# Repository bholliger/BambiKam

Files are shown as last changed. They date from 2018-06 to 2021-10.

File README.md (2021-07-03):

# BambiKam

> Quicklinks zu den aktuellen Versionen:
> - [BambiKam Easy V8.11](BambiKamEasy/BambiKamEasyV8.11)

- [BambiKam für DJI Mavic Pro (Platinum)](#bambikam-für-dji-mavic-pro-platinum)
- [BambiKam für DJI Mavic 2 Pro/Zoom](#bambikam-für-dji-mavic-2-prozoom)
- [Was ist BambiKam?](#was-ist-bambikam)
- [Zeig her die Bilder! Ich will sehen wie's aussieht!](#zeig-her-die-bilder-ich-will-sehen-wies-aussieht)
  - [Bilder der BambiKam Easy](#bilder-der-bambikam-easy)
- [Was zeichnet BambiKam aus?](#was-zeichnet-bambikam-aus)
  - [BambiKam Easy](#bambikam-easy)
- [Müssen an der Mavic 1 Modifikationen vorgenommen werden?](#müssen-an-der-mavic-1-modifikationen-vorgenommen-werden)
- [Kann die BambiKam Easy auch an die Mavic 2 befestigt werden?](#kann-die-bambikam-easy-auch-an-die-mavic-2-befestigt-werden)
- [Versionen](#versionen)
  - [Archiv](#archiv)
- [Warum sieht die BambiKam Easy so spartanisch aus?](#warum-sieht-die-bambikam-easy-so-spartanisch-aus)
- [Lizenz](#lizenz)

## BambiKam für DJI Mavic Pro (Platinum)

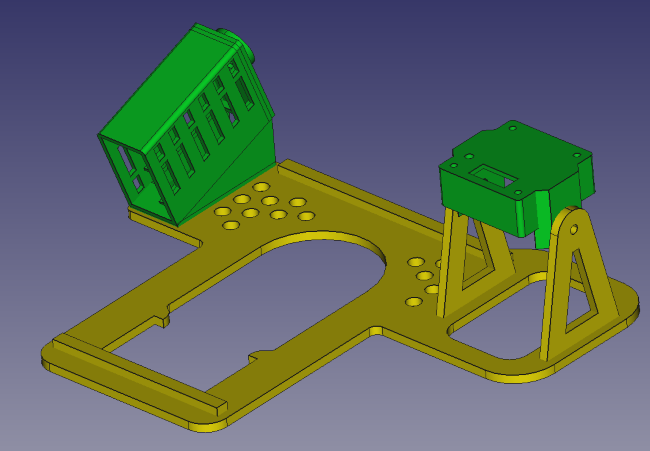
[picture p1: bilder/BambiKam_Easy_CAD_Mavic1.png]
Bild der BambiKam


## BambiKam für DJI Mavic 2 Pro/Zoom

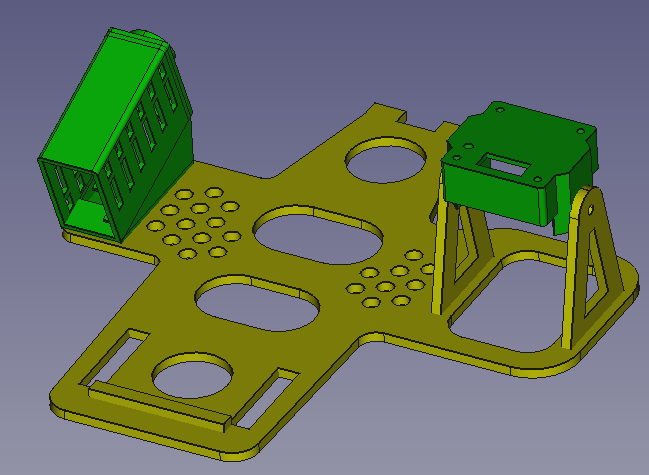
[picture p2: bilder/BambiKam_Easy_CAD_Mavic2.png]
Bild der BambiKam


## Was ist BambiKam?

BambiKam ist eine Plattform, welche es erlaubt eine [FLIR BOSON](http://www.flir.de/cores/boson/) Wärmebildkamera zusammen mit einem [Eachine TX801-Sender](https://www.google.com/search?q=eachine%20tx801) und einer [Cloverleaf](https://www.google.com/search?q=align+cloverleaf+5.8+ghz)-Antenne an eine [DJI Mavic Pro/Platinum](https://www.google.com/search?q=dji+mavic+pro+platinum) oder an eine [DJI Mavic 2 Pro/Zoom](https://www.google.com/search?q=dji+mavic+2+pro) zu befestigen.

Wahlweise ist es auch möglich, einen [SpeedyBee VTX-DVR](https://www.speedybee.com/speedy-bee-vtx-dvr/)-Transmitter zu verwenden. Dieser erlaubt es, das Videosignal direkt auf eine MicroSD-Karte aufzuzeichnen. Dazu muss das alternative Gehäuse verwendet werden. Die Grundplatte ist identisch.  (Hinweis: Dieser Transmitter hatte zu wenig Absatz und wird deshalb von der Herstellerfirma nicht mehr produziert.)

## Zeig her die Bilder! Ich will sehen wie's aussieht!

### Bilder der BambiKam Easy

[Bilder der BambiKam Easy](BambiKamEasy/BambiKamEasyV8.11#zeig-her-die-bilder-ich-will-sehen-wies-aussieht)

## Was zeichnet BambiKam aus?

### BambiKam Easy

- Inklusive Kamera, Sender und Antenne beträgt das Gewicht weniger als 65 Gramm.
- Durch das Anbringen der Kamera, Sender und Antenne auf der Seite kann auf Fussverlängerungen verzichtet werden. Dies spart ebenfalls Gewicht und macht die Drohne nicht höher.
- Durch die einfache Befestigung der Grundplatte an den hinteren Landekufen der Mavic ist es ganz einfach, die BambiKam zu entfernen und die Drohne als ganz normale Drohne zu verwenden.
- Die Grundplatte hat Löcher, welche die Sensoren der Mavic nicht beeinträchtigen. So ist es möglich, auch nach dem Anbringen der BambiKam, die Mavic mit Hilfe der Sensoren zu landen.

## Müssen an der Mavic 1 Modifikationen vorgenommen werden?

Jein. Durch die Tatsache, dass eine separate Stromversorgung wiederum Gewicht bedeutet und schon eine Stromversorgung der Drohne vorhanden ist, welche verwendet werden kann, um den Sender und die Kamera mit Strom zu versorgen, ist es eine Überlegung wert, die Stromversorgung des Quadcopters anzuzapfen. Selbstverständlich muss man sich der Tatsache bewusst sein, dass dies Auswirkung auf die Herstellergarantie haben kann.

Der Stromverbrauch des Senders und der Kamera ist sehr klein und beeinflusst die Flugzeit minimal.

Die BambiKam Easy sieht keine Halterung für einen separaten Akku vor.

Es besteht jedoch die Möglichkeit, dass auf den Akku der Mavic noch ein separater Akku aufgeklebt wird. Dieser Akku würde dann für die Speisung des Transmitters und der Wärmebildkamera zuständig sein.

## Kann die BambiKam Easy auch an die Mavic 2 befestigt werden?

Ja, die BambiKam Easy ist auch an die die Mavic 2 angepasst. Der Strom kann direkt vom Kopter bezogen werden und es sind keine Eingriffe in den Kopter nötig.

## Versionen

Die BambiKam wird stetig weitergepflegt. Folgende Versionen sind bisher erschienen:

- [BambiKam Easy V8.11](/BambiKamEasy/BambiKamEasyV8.11): Die Grundplatte wurde überarbeitet.

### Archiv

- [BambiKam Easy V5](/BambiKamEasy/BambiKamEasyV5): Erste veröffentlichte Version. Senkrechte, fixe Kameraeinstellung.
- [BambiKam Easy V6](/BambiKamEasy/BambiKamEasyV6): Kameraeinstellung kann bis 10° geneigt werden.
- [BambiKam Easy V8](/BambiKamEasy/BambiKamEasyV8): Das Transmittergehäuse wurde überarbeitet und wird direkt auf die Grundplatte aufgeklebt. Die Lüftung des Transmitters wurde ebenfalls verbessert. Die Löcher für die Ultraschall-Sensoren und Kameras wurden vergrössert.
- [BambiKam Easy V8.10](/BambiKamEasy/BambiKamEasyV8.10): Die Grundplatte wurde überarbeitet.- [BambiKam Pro V2](/BambiKamPro/BambiKamProV2): Aufhängung für 2-Achsen-Gimbal

## Warum sieht die BambiKam Easy so spartanisch aus?

> "Perfektion ist nicht dann erreicht, wenn es nichts mehr hinzuzufügen gibt, sondern wenn man nichts mehr weglassen kann."

-- <cite> Antoine de Saint-Exupéry, Terre des Hommes, III: L'Avion, p. 60 (1939)</cite>

Treffender kann man es nicht beschreiben.

## Lizenz

BambiKam steht unter der Lizenz [CC BY SA](https://creativecommons.org/licenses/by-sa/3.0/ch/) und darf somit beliebig kopiert, verändert und geteilt werden unter der Bedingung, dass diese Änderungen wiederum geteilt werden und ein Hinweis auf das Ursprungsprojekt gegeben wird.

Es wird keine Verantwortung übernommen.

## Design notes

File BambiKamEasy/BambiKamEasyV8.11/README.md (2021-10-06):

# BambiKam Easy V8.11 03.07.2021

> Bitte folgende Punkte beachten: [Wichtige/wissenswerte Punkte](#wichtigewissenswerte-punkte)

> Wo möchten Sie einsteigen?
> - [Bausatz zusammenbauen](#bausatz-zusammenbauen)
> - [Montage der Kamera (Endmontage)](#montage-der-kamera-endmontage)

- [BambiKam für DJI Mavic Pro (Platinum)](#bambikam-für-dji-mavic-pro-platinum)
- [BambiKam für DJI Mavic 2 Pro/Zoom](#bambikam-für-dji-mavic-2-prozoom)
- [Was ist BambiKam?](#was-ist-bambikam)
- [Warum wurde BambiKam Easy entworfen?](#warum-wurde-bambikam-easy-entworfen)
- [Zeig her die Bilder! Ich will sehen wie's aussieht!](#zeig-her-die-bilder-ich-will-sehen-wies-aussieht)
- [Was zeichnet BambiKam Easy aus?](#was-zeichnet-bambikam-easy-aus)
- [Müssen an der Mavic 1 Modifikationen vorgenommen werden?](#müssen-an-der-mavic-1-modifikationen-vorgenommen-werden)
- [Kann die BambiKam Easy auch an die Mavic 2 befestigt werden?](#kann-die-bambikam-easy-auch-an-die-mavic-2-befestigt-werden)
- [Lizenz](#lizenz)
- [Konfiguration der BambiKam Easy](#konfiguration-der-bambikam-easy)
- [Materialien](#materialien)
  - [Aviatik-Sperrholz 2mm](#aviatik-sperrholz-2mm)
  - [3D-Druck](#3d-druck)
- [Anfertigen der BambiKam Easy](#anfertigen-der-bambikam-easy)
  - [DJI Mavic Pro/Platinum mit FLIR Boson 320 50° oder 34°-Kamera](#dji-mavic-proplatinum-mit-flir-boson-320-50-oder-34-kamera)
    - [Lasern von Aviatik-Sperrholz 2mm für DJI Mavic Pro/Platinum mit FLIR Boson 320 50° oder 34°-Kamera](#lasern-von-aviatik-sperrholz-2mm-für-dji-mavic-proplatinum-mit-flir-boson-320-50-oder-34-kamera)
    - [3D-Druck des Splintens für die Befestigung an der Mavic 1](#3d-druck-des-splintens-für-die-befestigung-an-der-mavic-1)
  - [DJI Mavic 2 Pro/Zoom mit FLIR Boson 320 50° oder 34°-Kamera](#dji-mavic-2-prozoom-mit-flir-boson-320-50-oder-34-kamera)
    - [Lasern von Aviatik-Sperrholz 2mm für DJI Mavic 2 Pro/Zoom mit FLIR Boson 320 50° oder 34°-Kamera](#lasern-von-aviatik-sperrholz-2mm-für-dji-mavic-2-prozoom-mit-flir-boson-320-50-oder-34-kamera)
    - [3D-Druck des Splintens für die Befestigung an der Mavic 2](#3d-druck-des-splintens-für-die-befestigung-an-der-mavic-2)
  - [DJI Mavic 2 Pro/Zoom mit Thermocam XT384](#dji-mavic-2-prozoom-mit-thermocam-xt384)
    - [Lasern von Aviatik-Sperrholz 2mm für DJI Mavic 2 Pro/Zoom mit Thermocam XT384](#lasern-von-aviatik-sperrholz-2mm-für-dji-mavic-2-prozoom-mit-thermocam-xt384)
    - [3D-Druck des Splintens für die Befestigung an der Mavic 2](#3d-druck-des-splintens-für-die-befestigung-an-der-mavic-2-1)
  - [Kamerahalterung drucken](#kamerahalterung-drucken)
    - [Kamerahalterung drucken für die FLIR Boson 320 50° oder 34°-Kamera und dem Low Profile BOSON VPC Interface Module](#kamerahalterung-drucken-für-die-flir-boson-320-50-oder-34-kamera-und-dem-low-profile-boson-vpc-interface-module)
  - [Gehäuse für Transmitter drucken](#gehäuse-für-transmitter-drucken)
    - [Gehäuse für Eachine TX801](#gehäuse-für-eachine-tx801)
    - [Gehäuse für SpeedyBee VTX-DVR](#gehäuse-für-speedybee-vtx-dvr)
    - [Gehäuse für TBS Unify Pro 5G8 HV](#gehäuse-für-tbs-unify-pro-5g8-hv)
- [Bausatz zusammenbauen](#bausatz-zusammenbauen)
  - [Abstandhalter auf Grundplatte (Mitte)](#abstandhalter-auf-grundplatte-mitte)
  - [Aufhängung für die Kamera (Rechts)](#aufhängung-für-die-kamera-rechts)
  - [Lackieren der BambiKam Easy](#lackieren-der-bambikam-easy)
  - [Anbringen des Transmittergehäuses](#anbringen-des-transmittergehäuses)
    - [Transmittergehäuse für den Eachine TX801-Transmitter](#transmittergehäuse-für-den-eachine-tx801-transmitter)
    - [Transmittergehäuse für den SpeedyBee VTX-DVR-Transmitter](#transmittergehäuse-für-den-speedybee-vtx-dvr-transmitter)
    - [Transmittergehäuse für den TBS Unify Pro 5G8 HV](#transmittergehäuse-für-den-tbs-unify-pro-5g8-hv)
    - [Löten der Verbindungskabel für den TX801-Transmitter](#löten-der-verbindungskabel-für-den-tx801-transmitter)
    - [Löten der Verbindungskabel für den SpeedyBee VTX-DVR-Transmitter](#löten-der-verbindungskabel-für-den-speedybee-vtx-dvr-transmitter)
    - [Löten der Verbindungskabel für den TBS Unify Pro 5G8 HV-Transmitter](#löten-der-verbindungskabel-für-den-tbs-unify-pro-5g8-hv-transmitter)
    - [Löten der Verbindungskabel für den TX801-Transmitter (XT384-Kamera)](#löten-der-verbindungskabel-für-den-tx801-transmitter-xt384-kamera)
  - [Verlegen der Kabel](#verlegen-der-kabel)
  - [Sender und Antenne montieren](#sender-und-antenne-montieren)
- [Montage der Kamera (Endmontage)](#montage-der-kamera-endmontage)
  - [Kamera montieren](#kamera-montieren)
- [Anbringen der Grundplatte an den Kopter](#anbringen-der-grundplatte-an-den-kopter)
- [Fliegen](#fliegen)
- [Wichtige/wissenswerte Punkte](#wichtigewissenswerte-punkte)
- [Testflug mit der BambiKam V6](#testflug-mit-der-bambikam-v6)

## BambiKam für DJI Mavic Pro (Platinum)

Bild der BambiKam

## BambiKam für DJI Mavic 2 Pro/Zoom

Bild der BambiKam

## Was ist BambiKam?

BambiKam ist eine Plattform, welche es erlaubt eine [FLIR BOSON](http://www.flir.de/cores/boson/) Wärmebildkamera zusammen mit einem [Eachine TX801-Sender](https://www.google.com/search?q=eachine%20tx801) und einer [Cloverleaf](https://www.google.com/search?q=align+cloverleaf+5.8+ghz)-Antenne an eine [DJI Mavic Pro/Platinum](https://www.google.com/search?q=dji+mavic+pro+platinum) oder an eine [DJI Mavic 2 Pro/Zoom](https://www.google.com/search?q=dji+mavic+2+pro) zu befestigen.

Wahlweise ist es auch möglich, einen [SpeedyBee VTX-DVR](https://www.speedybee.com/speedy-bee-vtx-dvr/)-Transmitter zu verwenden. Dieser erlaubt es, das Videosignal direkt auf eine MicroSD-Karte aufzuzeichnen. Dazu muss das alternative Gehäuse verwendet werden. Die Grundplatte ist identisch. (Hinweis: Dieser Transmitter hatte zu wenig Absatz und wird deshalb von der Herstellerfirma nicht mehr produziert.)

## Warum wurde BambiKam Easy entworfen?

BambiKam Easy wurde für die Rehkitzsuche (siehe auch [Rehkitzrettung Schweiz](https://www.rehkitzrettung.ch/)) entworfen. Damit die Mavic mit dem Velo transportiert werden könnte, ist es wichtig, dass sie nicht mehr Platz braucht als wirklich nötig. Die Mavic kann so im nicht gefalteten Zustand in einen Koffer verstaut werden.

## Zeig her die Bilder! Ich will sehen wie's aussieht!

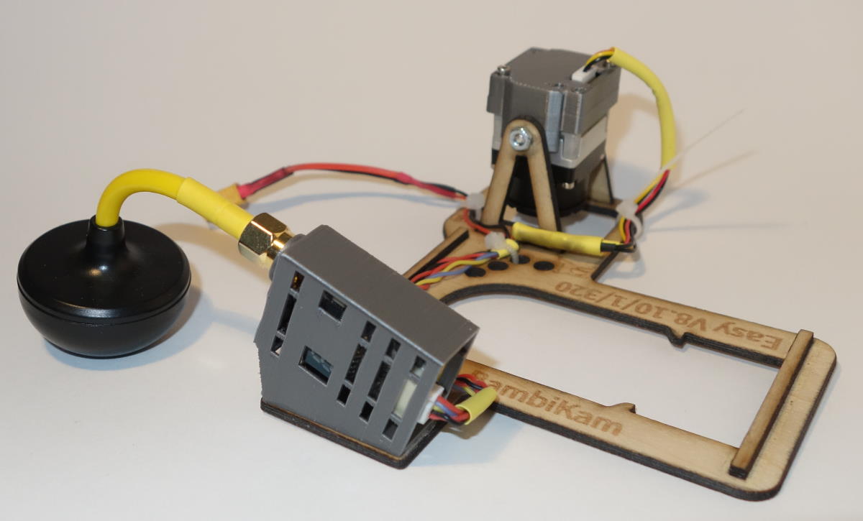
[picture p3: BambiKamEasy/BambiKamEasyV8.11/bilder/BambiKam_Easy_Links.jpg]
Links

BambiKam Easy für DJI Mavic Pro (oder Platinum), FLIR Boson 320/50°-Wärmebildkamera, Eachine TX801-Transmitter und direktem Stromanschluss an die angepasste Mavic.

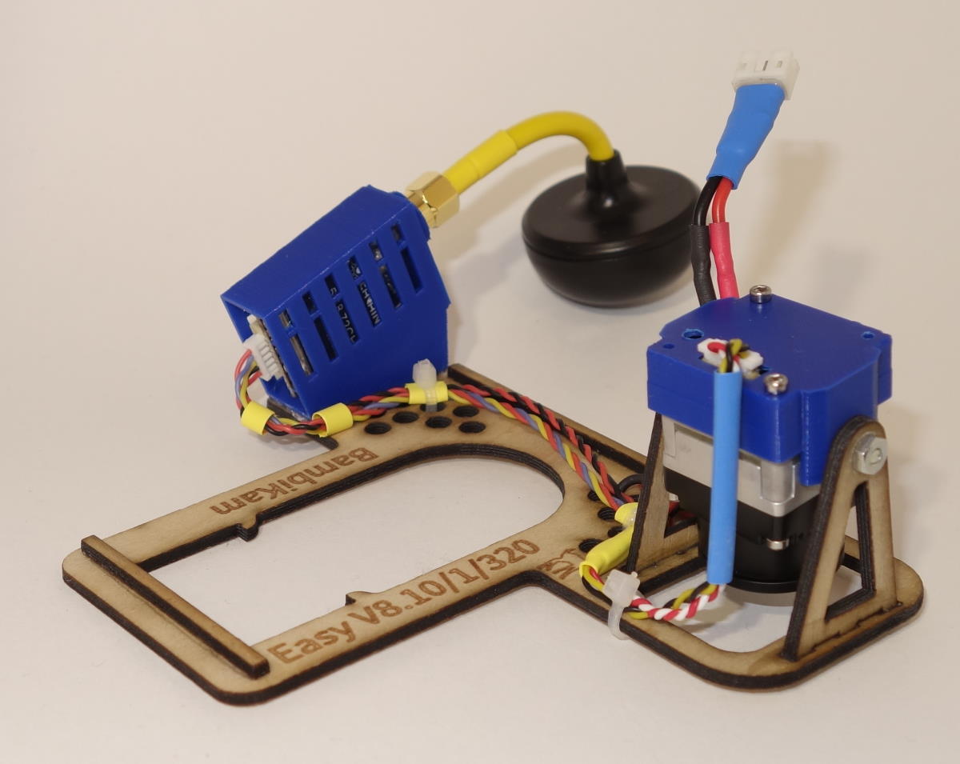
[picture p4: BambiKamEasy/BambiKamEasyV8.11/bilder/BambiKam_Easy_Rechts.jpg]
Rechts

BambiKam Easy für DJI Mavic Pro (oder Platinum), FLIR Boson 320/50°-Wärmebildkamera, Eachine TX801-Transmitter und Speisung via Akkus.

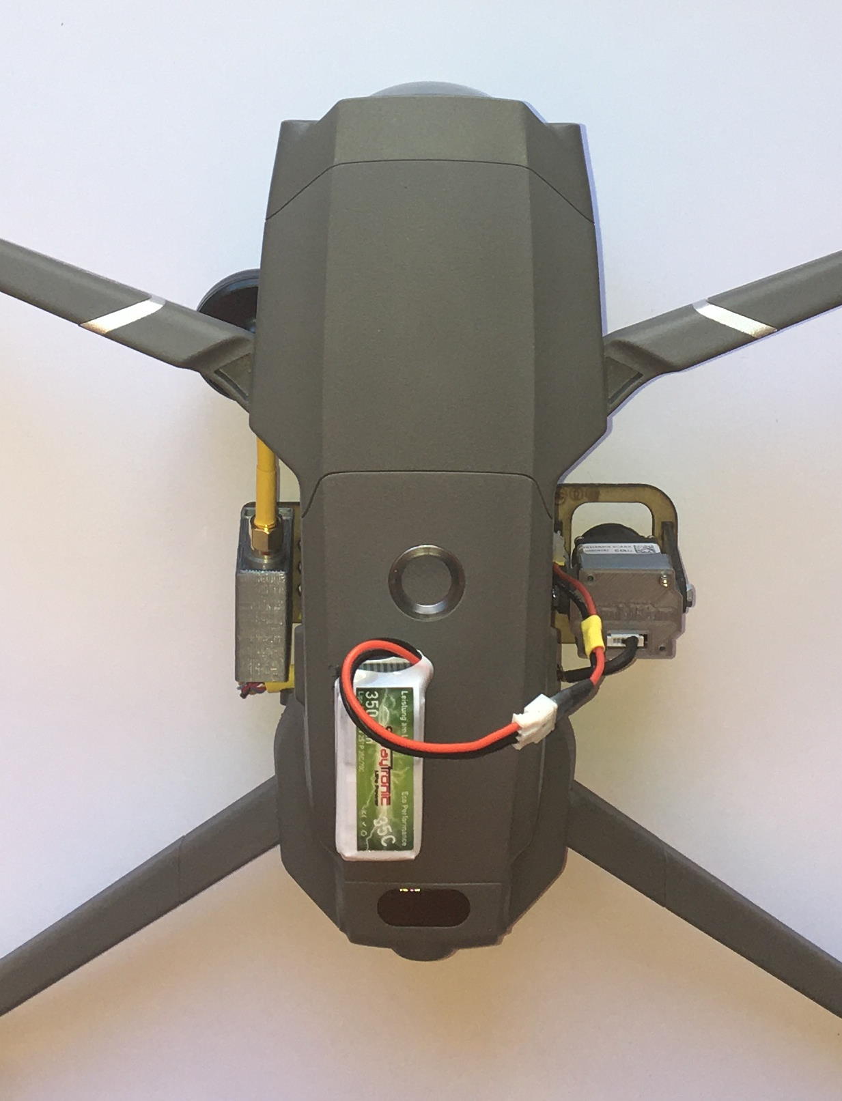
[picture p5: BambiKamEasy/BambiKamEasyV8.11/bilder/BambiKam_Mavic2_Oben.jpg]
Rechts mit Drohne


BambiKam Easy für DJI Mavic 2 Pro/Zoom, FLIR Boson 320/50°-Wärmebildkamera, Eachine TX801-Transmitter und Speisung via Akkus.

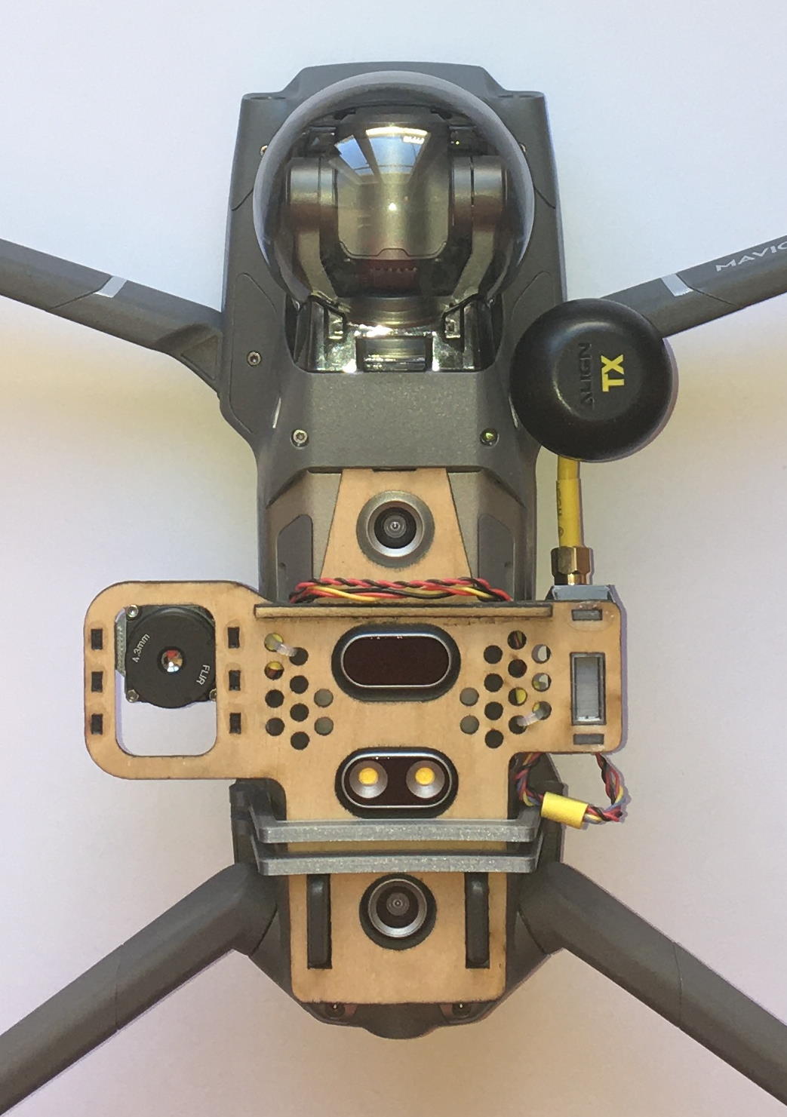
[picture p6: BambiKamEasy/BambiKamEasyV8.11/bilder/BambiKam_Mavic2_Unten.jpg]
Unten mit Drohne


BambiKam Easy für DJI Mavic 2 Pro/Zoom, FLIR Boson 320/50°-Wärmebildkamera, Eachine TX801-Transmitter und Speisung via Akkus.

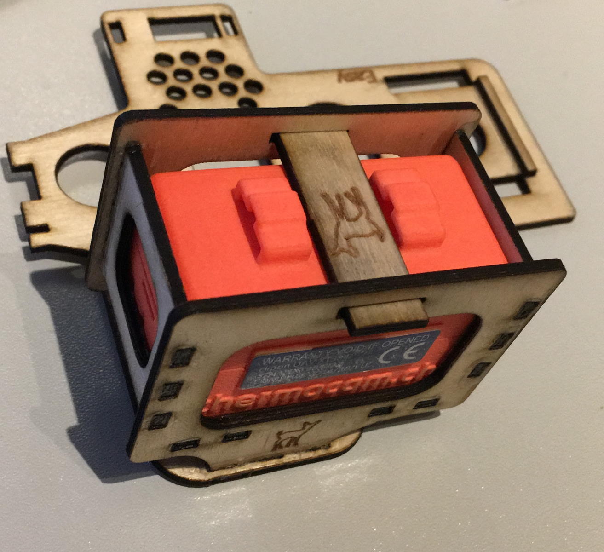
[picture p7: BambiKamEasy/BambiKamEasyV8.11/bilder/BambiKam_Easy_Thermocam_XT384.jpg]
Thermocam XT384


BambiKam Easy für DJI Mavic 2 Pro/Zoom, Thermocam XT384-Wärmebildkamera

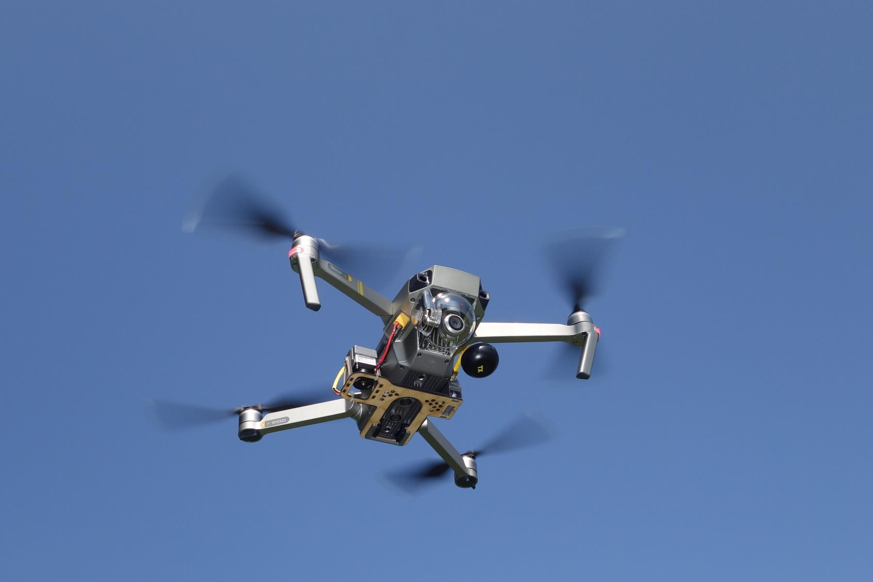
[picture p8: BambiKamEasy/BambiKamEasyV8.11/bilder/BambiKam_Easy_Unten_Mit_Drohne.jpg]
Fliegende Mavic 1


Fliegende DJI Mavic Pro Platinum mit BambiKam Easy und FLIR Boson 320/50°-Wärmebildkamera, Eachine TX801-Transmitter und direkter Stromversorgung.

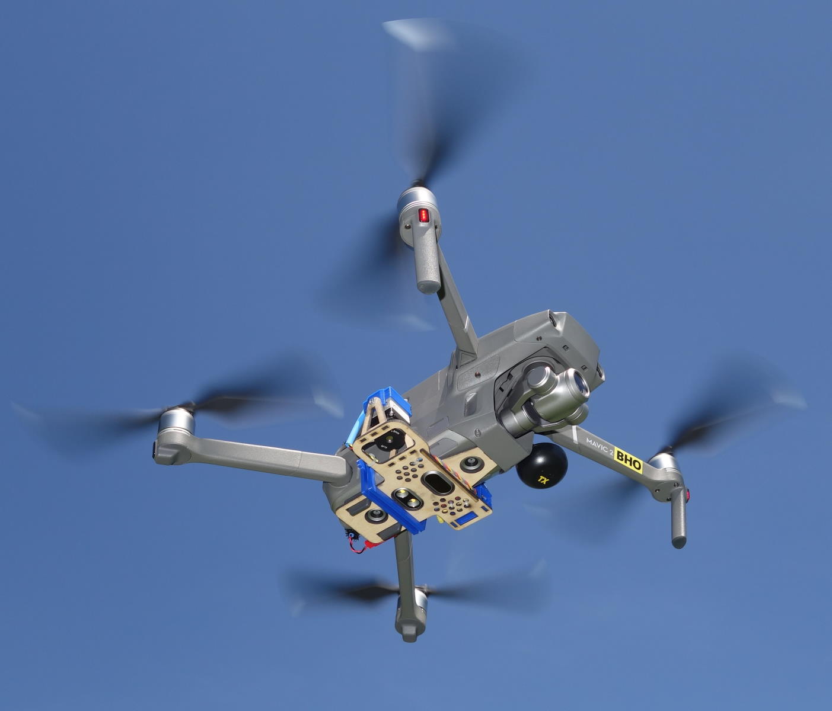
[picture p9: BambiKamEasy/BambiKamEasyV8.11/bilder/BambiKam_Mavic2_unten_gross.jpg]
Fliegende Mavic 2


Fliegende DJI Mavic 2 Zoom mit BambiKam Easy und FLIR Boson 320/50°-Wärmebildkamera, Eachine TX801-Transmitter und direkter Stromversorgung.

## Was zeichnet BambiKam Easy aus?

- Inklusive Kamera, Sender und Antenne beträgt das Gewicht weniger als 65 Gramm.
- Durch das Anbringen der Kamera, Sender und Antenne auf der Seite kann auf Verlängerungen verzichtet werden. Dies spart ebenfalls Gewicht und macht die Drohne nicht höher.
- Durch die einfache Befestigung der Grundplatte an den hinteren Landekufen der Mavic ist es ganz einfach, die BambiKam Easy zu entfernen und diese so als ganz normale Drohne zu verwenden.
- Die Grundplatte hat Löcher, welche die Sensoren der Mavic nicht beeinträchtigen. So ist es möglich, auch nach dem Anbringen der BambiKam Easy, die Mavic mit Hilfe der Sensoren zu landen.

## Müssen an der Mavic 1 Modifikationen vorgenommen werden?

Jein. Durch die Tatsache, dass eine separate Stromversorgung wiederum Gewicht bedeutet und schon eine Stromversorgung der Drohne vorhanden ist, welche verwendet werden kann, um den Sender und die Kamera mit Strom zu versorgen, ist es eine Überlegung wert, die Stromversorgung des Quadcopters anzuzapfen. Selbstverständlich muss man sich der Tatsache bewusst sein, dass dies Auswirkung auf die Herstellergarantie haben kann.

Der Stromverbrauch des Senders und der Kamera ist sehr klein und beeinflusst die Flugzeit minimal.

Die BambiKam Easy sieht keine Halterung für einen separaten Akku vor.

Es besteht jedoch die Möglichkeit, dass auf den Akku der Mavic noch ein separater Akku aufgeklebt wird. Dieser Akku würde dann für die Speisung des Transmitters und der Wärmebildkamera zuständig sein.

Für eine separate Stromversorgung wären folgende Komponenten nötig:

- Akkus (Es wird empfholen, für jeden Mavic Akku ein kleiner Akku anzuschaffen): [https://www.swaytronic.ch/LiPo-Akku---Swaytronic/LiPo-Akku-2S-7-4V/2S-7-4V---35C---70C/swaytronic-lipo-2s-7-4v-350mah-35c-70c-jst-phr-3pt.html](https://www.swaytronic.ch/LiPo-Akku---Swaytronic/LiPo-Akku-2S-7-4V/2S-7-4V---35C---70C/swaytronic-lipo-2s-7-4v-350mah-35c-70c-jst-phr-3pt.html)
- Adapterkabel (Ein Adapterkabel wird auseinandergeschnitten und für die Speisung der BambiKam verwendet. Weitere werden benötigt fürs Laden (Maximal 4)). [https://www.swaytronic.ch/LiPo---Zubehoer/LiPo-Adapterkabel/adapterkabel-ph-3p-maennlich-zu-xh-3p-weiblich-2s.html](https://www.swaytronic.ch/LiPo---Zubehoer/LiPo-Adapterkabel/adapterkabel-ph-3p-maennlich-zu-xh-3p-weiblich-2s.html)
- Verlängerungskabel (Damit die Akkus auf dem Akku kleben bleiben können, wird empfohlen, ein zusätzliches Verlängerungskabel pro Ladeplatz anzuschaffen (Maximal 4).) [https://www.swaytronic.ch/LiPo---Zubehoer/Balancer-Verlaengerungskabel/XH/balancer-verlaengerung-xh-10cm-2s.html](https://www.swaytronic.ch/LiPo---Zubehoer/Balancer-Verlaengerungskabel/XH/balancer-verlaengerung-xh-10cm-2s.html)
- Ladegerät (Ermöglicht das Laden der kleinen LiPo-Akkus.) [https://www.swaytronic.ch/Ladegeraete/Ladegeraete-12V-DC/ups4-ac-dc-charger.html](https://www.swaytronic.ch/Ladegeraete/Ladegeraete-12V-DC/ups4-ac-dc-charger.html)

## Kann die BambiKam Easy auch an die Mavic 2 befestigt werden?

Ja, die BambiKam Easy ist auch an die die Mavic 2 angepasst. Der Strom kann direkt vom Kopter bezogen werden und es sind keine Eingriffe in den Kopter nötig.

## Lizenz

BambiKam Easy steht unter der Lizenz [CC BY SA](https://creativecommons.org/licenses/by-sa/3.0/ch/) und darf somit beliebig kopiert, verändert und geteilt werden unter der Bedingung, dass diese Änderungen wiederum geteilt werden und ein Hinweis auf das Ursprungsprojekt gegeben wird.

Es wird keine Verantwortung übernommen.

## Konfiguration der BambiKam Easy

Die BambiKam Easy kann für verschiedene Quadcopter, Kameras und Transmitter aufgebaut werden:

Quadcopter

- [DJI Mavic Pro](https://www.dji.com/mavic)
- [DJI Mavic Pro Platinum](https://www.dji.com/mavic-pro-platinum)
- [DJI Mavic 2 Pro](https://www.dji.com/mavic-2)
- [DJI Mavic 2 Zoom](https://www.dji.com/mavic-2)

Kameras [FLIR BOSON](http://www.flir.de/cores/boson/)

- FLIR Boson 320 50°
- FLIR Boson 320 34°
- Thermocam XT384

[Low Profile BOSON VPC Interface Module](https://www.oemcameras.com/rhp-bos-vpc-if.htm)

Einfaches Interface, welches das Bild der Kamera in ein Analogsignal umwandelt und zum Transmitter überträgt.

Plattformwahl

Die oben angeführten Quadcopter- und Kamera-Modelle lassen sich mit insgesamt drei verschiedenen Plattformen abdecken. Für die zwei verschiedenen Mavic-Modelle sind die Ausschnitte der Landekufen und Sensoren unterschiedlich.

| | DJI Mavic Pro/Platinum | DJI Mavic 2 Pro/Zoom |
| --- | --- | --- |
| FLIR Boson 320 | [Link](#dji-mavic-proplatinum-mit-flir-boson-320-50-oder-34-kamera) | [Link](#dji-mavic-2-prozoom-mit-flir-boson-320-50-oder-34-kamera) |
| Thermocam XT384 | | [Link](#dji-mavic-2-prozoom-mit-thermocam-xt384) |

Transmitterwahl

Die Grundplatte kann drei verschiedene Transmittergehäuse aufnehmen. Die Wahl des Transmitters hat somit keine Auswirkung auf die Grundplatte.

- [Eachine TX801-Sender](https://www.google.com/search?q=eachine%20tx801)
- [SpeedyBee VTX-DVR](https://www.speedybee.com/speedy-bee-vtx-dvr/) (Hinweis: Wird nicht mehr hergestellt.)
- [TBS Unifiy Pro 5G8](https://www.team-blacksheep.com/products/prod:unify_pro_hv)

## Materialien

### Aviatik-Sperrholz 2mm

Der Hauptteil besteht aus Aviatik Sperrholz, 2mm. Dieses erhält man bei Coop Bau&Hobby.
Das Aviatik Sperrholz hat den Vorteil, dass es dünn, sehr stabil und vielschichtig verleimt ist.

### 3D-Druck

Die Kamerahalterung und das Gehäuse für den Transmitter werden im 3D-Druckverfahren hergestellt.

## Anfertigen der BambiKam Easy

Ist das Holz beschafft, so lässt sich die Form sehr einfach mit einem LaserCutter schneiden.

Beispielsweise verfügen diverse Fablabs in der Schweiz über einen Lasercutter [Fablabs der Schweiz](https://fablab.ch/#/machine).
So auch das [FablabWinti](https://www.fablabwinti.ch/das-lab/ausstattung/lasercutter/). (Neue Mitglieder sind immer herzlich willkommen!)

### DJI Mavic Pro/Platinum mit FLIR Boson 320 50° oder 34°-Kamera

#### Lasern von Aviatik-Sperrholz 2mm für DJI Mavic Pro/Platinum mit FLIR Boson 320 50° oder 34°-Kamera



Das SVG [BambiKam_Easy_Aviatik_Sperrholz_2mm_Mavic_ProPlatinum_320.svg](plan/BambiKam_Easy_Aviatik_Sperrholz_2mm_Mavic_ProPlatinum_320.svg) soll folgendermassen gelasert werden:

| Reihenfolge | Farbe | Geschwindigkeit | Intensität |
| --- | --- | --- | --- |
| 1 | Grün | 1000 | 3% |
| 2 | Pink | 1000 | 65% |
| 3 | Schwarz | 1000 | 65% |
| 4 | Rot | ignorieren | ignorieren |

> Bitte beachten, dass die Holzmaserung gemäss dem roten Pfeil ausgerichtet wird.

#### 3D-Druck des Splintens für die Befestigung an der Mavic 1

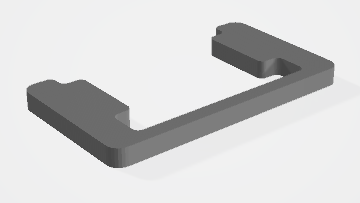
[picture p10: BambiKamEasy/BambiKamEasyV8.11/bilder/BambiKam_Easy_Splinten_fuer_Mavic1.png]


Das STL für den Druck des Splintens [BambiKam_Easy_Splinten_fuer_Mavic1](plan/BambiKam_Easy_Splinten_fuer_Mavic1.stl) kann mit dem 3D-Drucker ausgedruckt werden.

### DJI Mavic 2 Pro/Zoom mit FLIR Boson 320 50° oder 34°-Kamera

#### Lasern von Aviatik-Sperrholz 2mm für DJI Mavic 2 Pro/Zoom mit FLIR Boson 320 50° oder 34°-Kamera



Das SVG [BambiKam_Easy_Aviatik_Sperrholz_2mm_Mavic_2_320.svg](plan/BambiKam_Easy_Aviatik_Sperrholz_2mm_Mavic_2_320.svg) soll folgendermassen gelasert werden:

| Reihenfolge | Farbe | Geschwindigkeit | Intensität |
| --- | --- | --- | --- |
| 1 | Grün | 1000 | 3% |
| 2 | Pink | 1000 | 65% |
| 3 | Schwarz | 1000 | 65% |
| 4 | Rot | ignorieren | ignorieren |

> Bitte beachten, dass die Holzmaserung gemäss dem roten Pfeil ausgerichtet wird.
#### 3D-Druck des Splintens für die Befestigung an der Mavic 2

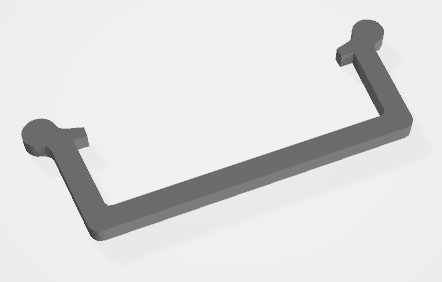
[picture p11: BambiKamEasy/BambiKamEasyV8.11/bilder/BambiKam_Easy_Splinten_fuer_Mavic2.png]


Das STL für den Druck des Splintens [BambiKam_Easy_Splinten_fuer_Mavic2](plan/BambiKam_Easy_Splinten_fuer_Mavic2.stl) kann mit dem 3D-Drucker ausgedruckt werden. Es können gleich zwei Exemplare zur Befestigung verwendet werden.

### DJI Mavic 2 Pro/Zoom mit Thermocam XT384

#### Lasern von Aviatik-Sperrholz 2mm für DJI Mavic 2 Pro/Zoom mit Thermocam XT384



Das SVG [BambiKam_Easy_Aviatik_Sperrholz_2mm_Mavic_2_Thermocam.svg](plan/BambiKam_Easy_Aviatik_Sperrholz_2mm_Mavic_2_Thermocam.svg) soll folgendermassen gelasert werden:

| Reihenfolge | Farbe | Geschwindigkeit | Intensität |
| --- | --- | --- | --- |
| 1 | Grün | 1000 | 3% |
| 2 | Pink | 1000 | 65% |
| 3 | Schwarz | 1000 | 65% |
| 4 | Rot | ignorieren | ignorieren |

> Bitte beachten, dass die Holzmaserung gemäss dem roten Pfeil ausgerichtet wird.

#### 3D-Druck des Splintens für die Befestigung an der Mavic 2



Das STL für den Druck des Splintens [BambiKam_Easy_Splinten_fuer_Mavic2](plan/BambiKam_Easy_Splinten_fuer_Mavic2.stl) kann mit dem 3D-Drucker ausgedruckt werden. Es können gleich zwei Exemplare zur Befestigung verwendet werden.

### Kamerahalterung drucken

#### Kamerahalterung drucken für die FLIR Boson 320 50° oder 34°-Kamera und dem Low Profile BOSON VPC Interface Module

Wichtig: Dieses Gehäuse ist für das Interface "Low Profile BOSON VPC Interface Module":

[https://www.oemcameras.com/rhp-bos-vpc-if.htm](https://www.oemcameras.com/rhp-bos-vpc-if.htm)

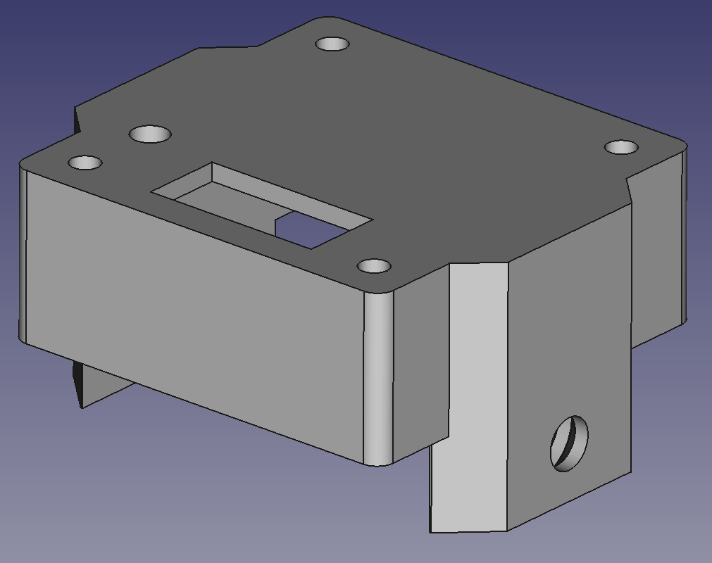
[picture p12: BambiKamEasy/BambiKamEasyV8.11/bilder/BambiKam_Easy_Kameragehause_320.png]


Das STL [BambiKam_Easy_Kameragehaeuse_3D-Druck_FLIR_BOSON_LowIF_320.stl](plan/BambiKam_Easy_Kameragehaeuse_3D-Druck_FLIR_BOSON_LowIF_320.stl) kann mit dem 3D-Drucker ausgedruckt werden.

### Gehäuse für Transmitter drucken

Die BambiKam Easy kann entweder mit dem Eachine TX801, mit dem SpeedyBee VTX-DVR oder TBS Unify Pro 5G8 HV ausgestattet werden.

#### Gehäuse für Eachine TX801

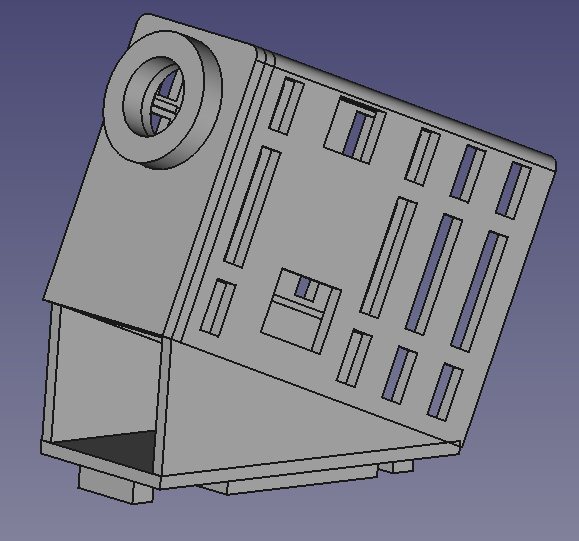
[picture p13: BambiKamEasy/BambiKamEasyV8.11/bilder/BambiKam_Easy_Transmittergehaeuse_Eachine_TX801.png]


Das STL [BambiKam_Easy_Transmittergehaeuse_Eachine_TX801_3D-Druck](plan/BambiKam_Easy_Transmittergehaeuse_Eachine_TX801_3D-Druck.stl) kann mit dem 3D-Drucker ausgedruckt werden.

#### Gehäuse für SpeedyBee VTX-DVR

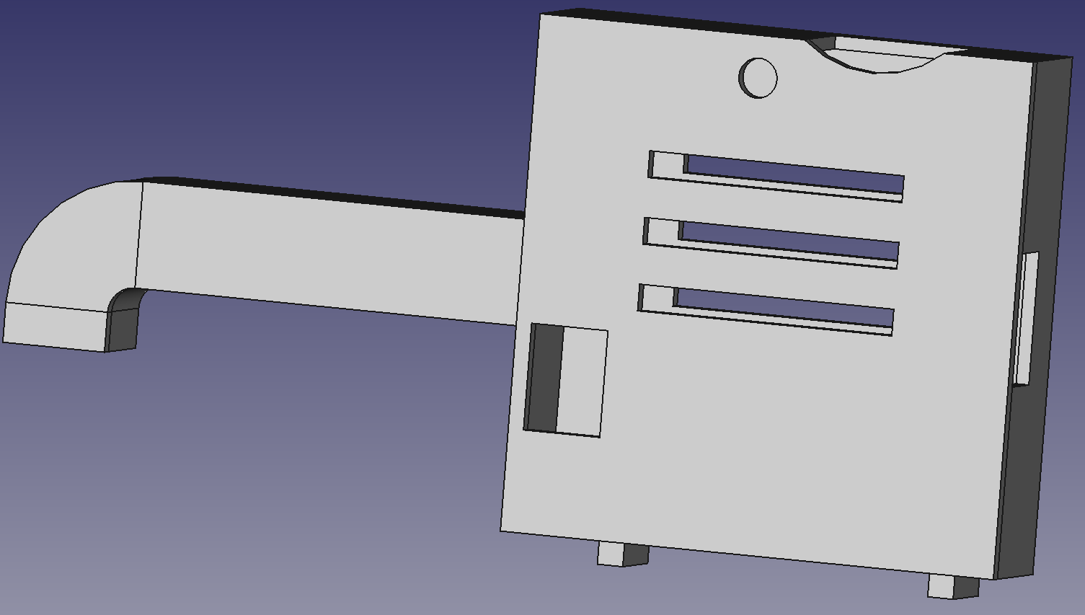
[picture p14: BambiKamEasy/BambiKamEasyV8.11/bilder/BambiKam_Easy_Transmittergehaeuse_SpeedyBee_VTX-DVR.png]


Das STL für den Boden [BambiKam_Easy_Transmittergehaeuse_SpeedyBee_VTX-DVR-Boden-3D-Druck](plan/BambiKam_Easy_Transmittergehaeuse_SpeedyBee_VTX-DVR-Boden-3D-Druck.stl) und jenes für den Deckel [BambiKam_Easy_Transmittergehaeuse_SpeedyBee_VTX-DVR-Deckel-3D-Druck](plan/BambiKam_Easy_Transmittergehaeuse_SpeedyBee_VTX-DVR-Deckel-3D-Druck.stl) kann mit dem 3D-Drucker ausgedruckt werden.

#### Gehäuse für TBS Unify Pro 5G8 HV

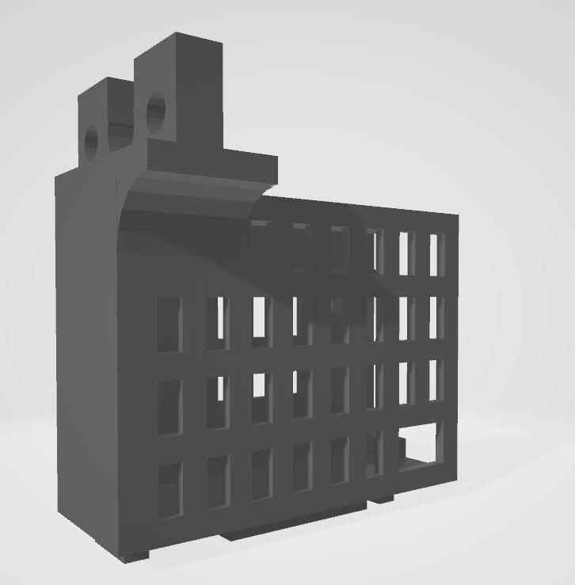
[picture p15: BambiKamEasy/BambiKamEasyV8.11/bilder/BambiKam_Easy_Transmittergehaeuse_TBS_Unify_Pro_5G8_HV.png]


Das STL [BambiKam_Easy_Transmittergehaeuse_TBS_Unify_Pro_5G8_HV_3D-Druck](plan/BambiKam_Easy_Transmittergehaeuse_TBS_Unify_Pro_5G8_HV_3D-Druck.stl) kann mit dem 3D-Drucker ausgedruckt werden.

## Bausatz zusammenbauen

Da die zu leimenden Elemente voneinander abhängen und relativ rasch halten müssen, empfiehlt es sich hier einen holztauglichen Sekundenleim zu verwenden.

Beispielsweise UHU blitzschnell Supergel oder Pattex Ultra Gel. Beide zeichnen sich dadurch aus, dass sie auch outdoortauglich sind und sehr gut halten.

Wichtig ist anschliessend, das verleimte Produkt an der Luft zu trocknen: So verbleiben keine weissen Absonderungen des Sekundenleimes am Holz.

### Abstandhalter auf Grundplatte (Mitte)

Die Abstandhalter stellen einen Abstand zur Drohne her, damit unter dieser die Luft etwas besser zirkulieren kann und zusätzlich die Kabel zwischen der Grundplatte und der Drohne durchgeführt werden können.

Die Orte, wo die Abstandhalter angebracht werden könnten, sind oben in den Bildern ersichtlich.

### Aufhängung für die Kamera (Rechts)

Die Stützen für das Kameragehäuse müssen im exakten Innen-Abstand von 27 mm zueinander eingeklebt werden, damit das Kameragehäuse aus dem 3D-Drucker darin Platz findet. Idealerweise montiert man das Kameragehäuse (ohne die Kamera einzubauen) bereits an die Stützen und hat so den perfekten Abstand.

Das Kameragehäuse wird mit zwei Senkkopfschrauben (M2.5, 6mm Länge) von innen her festgeschraubt. Die Muttern liegen aussen. Um die Kamera zu schonen, sollte diese erst später montiert werden. Die Muttern sollten mit etwas Loctite oder Ähnlichem gesichert werden.

### Lackieren der BambiKam Easy

Um das Holz vor Feuchtigkeit zu schützen, kann die BambiKam Easy noch mit einem schützenden Klarlack lackiert werden. Die allenfalls zuvor schon angebrachten Elemente sollten aber entfernt werden.

### Anbringen des Transmittergehäuses

#### Transmittergehäuse für den Eachine TX801-Transmitter

Das Transmittergehäuse für den TX801-Transmitter wird direkt auf die Grundplatte geklebt. Dabei zeigt das Loch für die Antenne nach vorne.

#### Transmittergehäuse für den SpeedyBee VTX-DVR-Transmitter

Das Transmittergehäuse für den SpeedyBee VTX-DVR-Transmitter wird mit dem Deckel nach aussen aufgeklebt. Die Antenne zeigt auch hier nach vorne.

#### Transmittergehäuse für den TBS Unify Pro 5G8 HV

Das Transmittergehäuse für den TBS Unify Pro 5G8 HV-Transmitter wird direkt auf die Grundplatte geklebt. Dabei zeigt die Aufnahme der Antenne nach vorne.

#### Löten der Verbindungskabel für den TX801-Transmitter

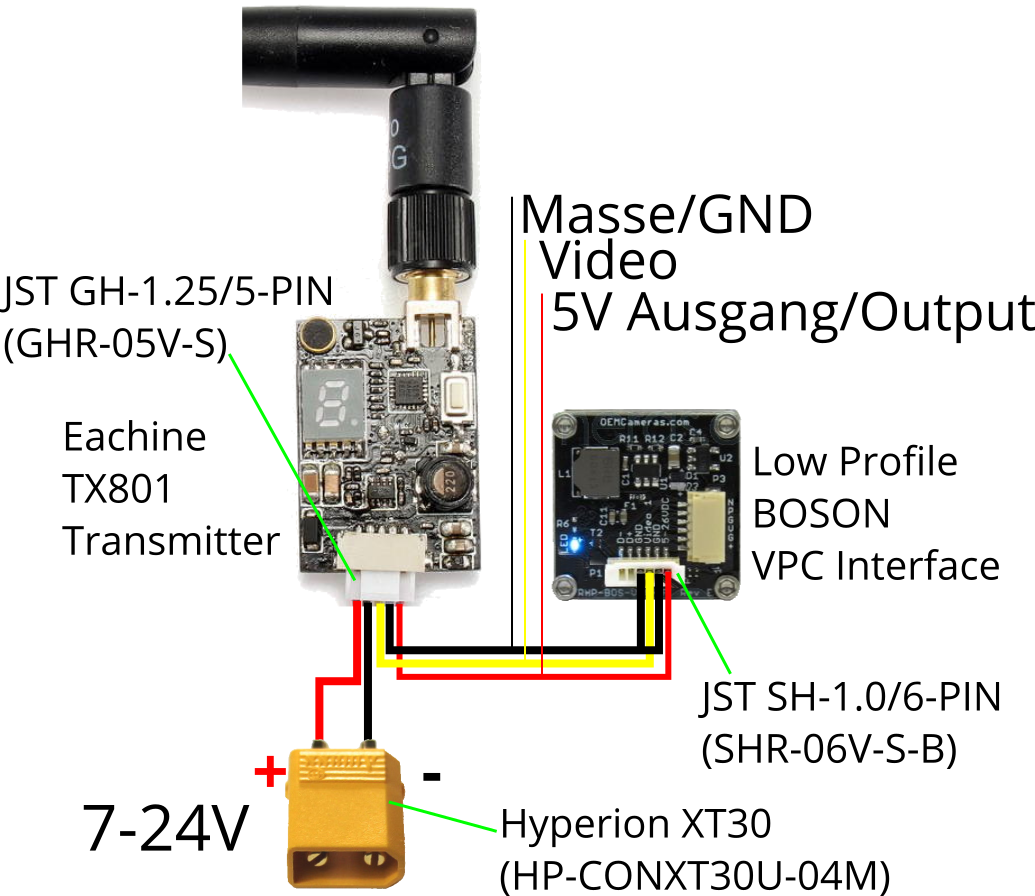
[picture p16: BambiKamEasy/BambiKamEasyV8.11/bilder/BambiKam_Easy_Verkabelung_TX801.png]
Verkabelung


Mit dem TX801-Transmitter wird ein Kabel mit einem JST GH 1.25 5-Pin-Stecker geliefert (links im Bild) und mit dem Interface ein Kabel mit einem JST SH 1.0 6-Pin-Stecker (rechts im Bild). Die beiden Kabel müssen wie im Bild aneinander gelötet werden. Die beiden Stromversorgungskabel (links unten im Bild) müssen womöglich noch etwas verlängert werden damit diese an der Drohne, welche für die Spannungsversorgung bereits vorbereitet wurde, eingesteckt werden können. Im Bild ist beispielhaft ein XT30-Stecker zu sehen.

#### Löten der Verbindungskabel für den SpeedyBee VTX-DVR-Transmitter

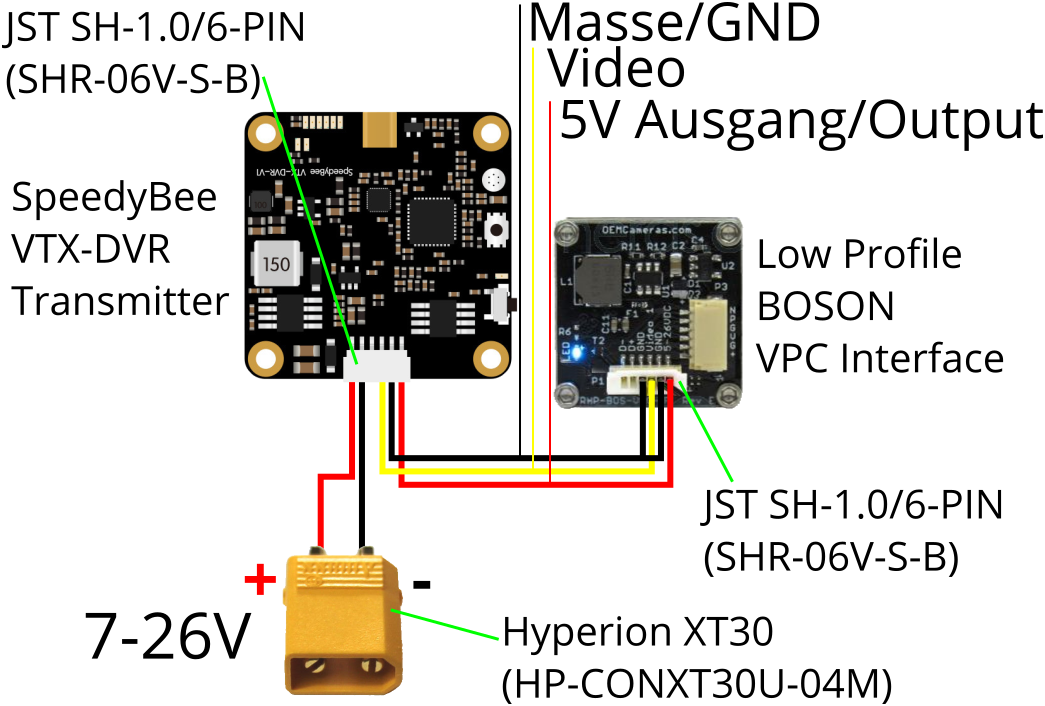
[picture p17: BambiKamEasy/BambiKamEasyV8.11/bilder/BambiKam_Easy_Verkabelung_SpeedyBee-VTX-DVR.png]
Verkabelung


Mit dem SpeedyBee VTX-DVR-Transmitter wird ein Kabel mit einem JST SH 1.0 6-Pin-Stecker geliefert (links im Bild) und mit dem Interface ein Kabel mit (ebenfalls) einem JST SH 1.0 6-Pin-Stecker (rechts im Bild). Die beiden Kabel müssen wie im Bild aneinander gelötet werden. Die beiden Stromversorgungskabel (links unten im Bild) müssen womöglich noch etwas verlängert werden damit diese an der Drohne, welche für die Spannungsversorgung bereits vorbereitet wurde, eingesteckt werden können. Im Bild ist beispielhaft ein XT30-Stecker zu sehen.

#### Löten der Verbindungskabel für den TBS Unify Pro 5G8 HV-Transmitter

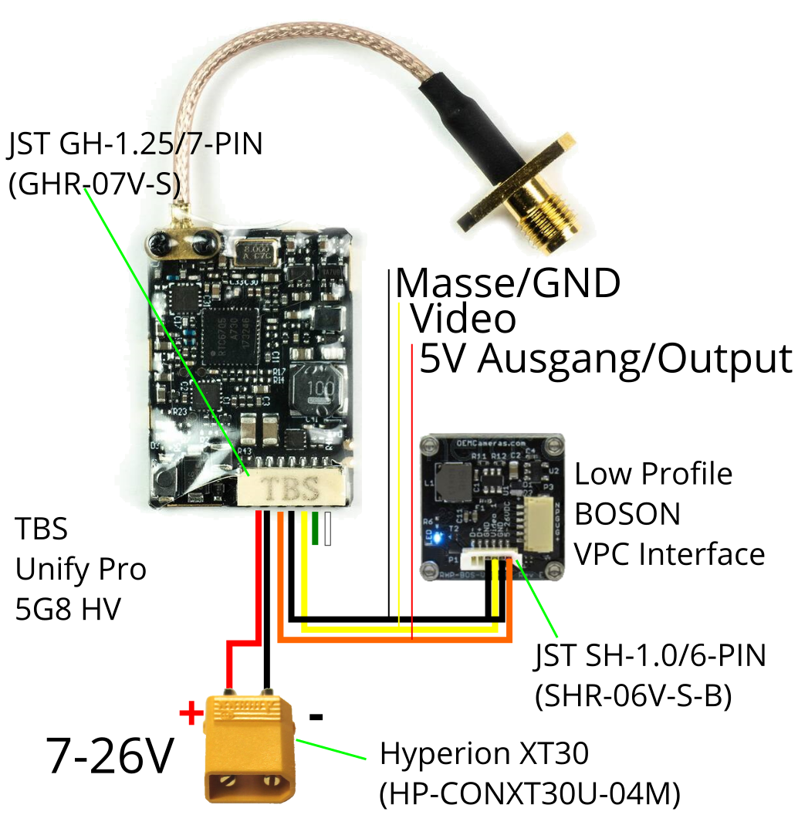
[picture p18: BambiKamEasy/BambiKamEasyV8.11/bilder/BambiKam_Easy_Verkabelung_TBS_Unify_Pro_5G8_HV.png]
Verkabelung


Mit dem TBS Unify Pro 5G8 HV-Transmitter wird ein Kabel mit einem JST GH 1.25 7-Pin-Stecker geliefert und mit dem Interface ein Kabel mit einem JST SH 1.0 6-Pin-Stecker (rechts im Bild). Die beiden Kabel müssen wie im Bild aneinander gelötet werden. Der angebrachte BEC-Stecker am Stromversorgungskabel kann direkt für die Versorgung verwendet werden. Im Bild ist beispielhaft ein XT30-Stecker zu sehen.

#### Löten der Verbindungskabel für den TX801-Transmitter (XT384-Kamera)

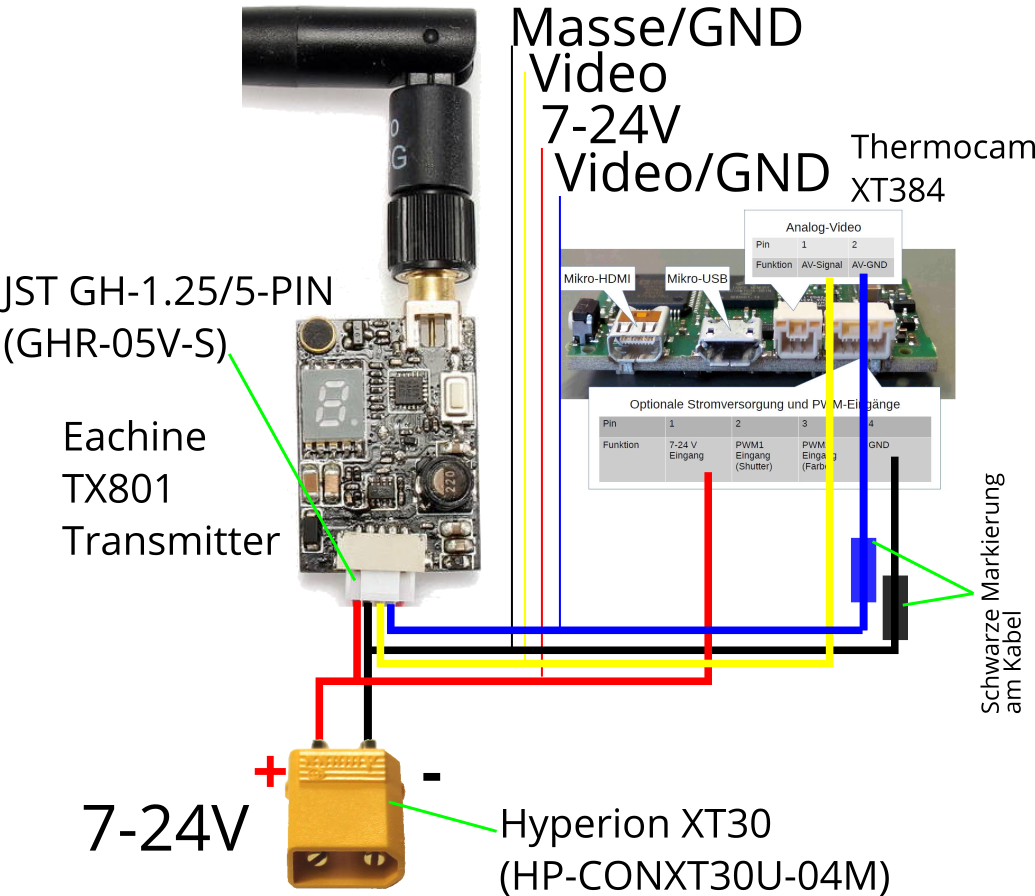
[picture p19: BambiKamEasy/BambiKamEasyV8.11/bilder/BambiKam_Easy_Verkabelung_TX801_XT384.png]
Verkabelung


Mit dem TX801-Transmitter wird ein Kabel mit einem JST GH 1.25 5-Pin-Stecker geliefert (links im Bild) und mit der XT384-Kamera zwei Kabel mit einem 4-Pin-Stecker und einem 2-Pin-Stecker (rechts im Bild). Die beiden Kabel müssen wie im Bild aneinander gelötet werden. Die beiden Stromversorgungskabel (links unten im Bild) müssen womöglich noch etwas verlängert werden damit diese an der Drohne, welche für die Spannungsversorgung bereits vorbereitet wurde, eingesteckt werden können. Im Bild ist beispielhaft ein XT30-Stecker zu sehen.

### Verlegen der Kabel

Die Kabel können (je nach Länge) nahe des oberen Abstandhalters entlang oder mittig, zwischen die zwei grossen Löcher, gelegt werden und der Einfachheit halber mit zwei kleinen Kabelbindern oder Flüssiggummi befestigt werden.

### Sender und Antenne montieren

>Es ist wichtig, dass die Antenne während des Betriebes nicht abfallen kann. Wird der Sender ohne Antenne betrieben, kann dieser beschädigt werden.

Der Sender wird in das Gehäuse eingeschoben, wobei darauf geachtet werden muss, dass die quadratische Fläche um das Antennengewinde plan mit dem Gehäuse ist. Die Antenne soll dabei nach vorne zeigen. Die Antenne muss anschliessend mit einem Schraubenschlüssel gut angezogen werden. Wichtig ist, dass sich die Antenne nicht mehr selbständig in der Fassung drehen kann.

## Montage der Kamera (Endmontage)

### Kamera montieren

Bevor die Kamera montiert werden kann, muss das Interface auf die Kamera aufgesteckt werden. Der Stecker ist nicht leichtgängig und es kann helfen, wenn man das Interface vorsichtig mit den kurzen Schrauben an der Kamera festschraubt.

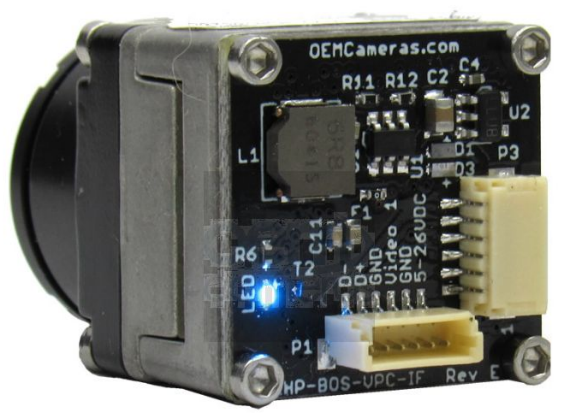
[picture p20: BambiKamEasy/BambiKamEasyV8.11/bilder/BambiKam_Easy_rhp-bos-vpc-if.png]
rhp-bos-vpc-if


Wenn kein Spalt mehr zwischen Interface und Kamera vorhanden ist, können die Schrauben wieder gelöst werden und die Kamera mit Interface in das Gehäuse auf der rechten Seite eingeschoben werden. Dabei ist darauf zu achten, dass die Ausrichtung des nach oben zeigenden Steckers des Interfaces korrekt ist.

Die Befestigung erfolgt mit den langen Schrauben, welche mit dem Interface mitgeliefert wurden.

Der Stecker des Kabels muss anschliessend noch auf dem Interface aufgesteckt werden.

## Anbringen der Grundplatte an den Kopter

Am besten legt man die Mavic auf den Rücken und legt die Grundplatte mit der Kamera nach unten zeigend so auf die Landekufen, dass sie durch die vertikalen Aussparungen zeigen. Die Befestigung der Grundplatte erfolgt durch das Einschieben des Splintens mit der Aussparung. Wichtig ist, dass der Splinten von links eingeschoben wird, da so die Kamera nicht verdeckt wird.

## Fliegen

Das Flugverhalten der Mavic wird durch das Mitführen der BambiKam Easy nicht merklich verändert. Der Start verläuft balanciert, da sich die Komponenten im Schwerpunkt befinden.

Durch das geringe Gewicht der BambiKam Easy wird auch die Flugzeit nicht allzu negativ beeinflusst.

## Wichtige/wissenswerte Punkte

- Der Sender darf *nie* ohne Antenne mit Strom versorgt werden, da sonst der Sender zerstört wird.
- Das an der Stromversorgung angehängte Kabel führt nur Strom, wenn die Drohne eingeschaltet ist. Ein Ein-/Aus-Schalter ist nicht nötig.
- Die Kunststoffteile sind aus PLA gefertigt. Bitte lassen Sie diese nicht im heissen Auto liegen, da es sonst allenfalls zu Verformungen kommen könnte.
- Es kann in seltenen Fällen vorkommen, dass sich die Ultraschallsensoren (Downward Vision Sensors) nicht mit der Aufhängung verstehen. Dies äussert sich so, dass die Mavic eigenständig aufsteigt. Dem muss durch beharrliches Gegensteuern (linker Steuerknüppel nach unten ziehen) begegnet werden. Falls das Problem nicht gelöst werden kann, so können die "Downward Vision Sensors" abgeschaltet werden. Dies bedeutet, man muss bei der Landung vorsichtiger sein, da man keine Unterstützung durch die Sensoren hat. Dies ist aber eigentlich nicht die Idee.

## Testflug mit der BambiKam V6

| | |
| --- | --- |
| Datum: | 19.08.2018 10:15 |
| Wetter: | Wolkenloser Himmel, 22°C, Wind 5 km/h |
| Testszenario: | Wiederholter Wegpunktflug des folgenden Tracks: <https://flylitchi.com/hub?m=hBNMMruee6#> |
| Zeitmessung: | Ab Start des 1. Missionsdurchganges (ein Meter ab Boden) bis zum Ertönen des Akku-Alarms (30%) |
| __Erreichte Zeit:__ | __17 Minuten 2 Sekunden__ (Vorwärtsflug) |

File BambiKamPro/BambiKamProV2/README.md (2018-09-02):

# BambiKam Pro V2 (BETA) 2.9.2018

> Wichtig: V2 ist derzeit noch im BETA-Stadium. Deshalb ist hier auch nocht fast nichts aktuell.

> Wo möchten Sie einsteigen?
> - [Kleben der einzelnen Elemente](#kleben-der-einzelnen-elemente)

- [Was ist BambiKam?](#was-ist-bambikam)
- [Zeig her die Bilder! Ich will sehen wie's aussieht!](#zeig-her-die-bilder-ich-will-sehen-wies-aussieht)
- [Was zeichnet BambiKam Pro aus?](#was-zeichnet-bambikam-pro-aus)
- [Müssen an der Drohne Modifikationen vorgenommen werden?](#m%C3%BCssen-an-der-drohne-modifikationen-vorgenommen-werden)
- [Lizenz](#lizenz)
- [Materialien](#materialien)
    - [Aviatik-Sperrholz 2mm](#aviatik-sperrholz-2mm)
    - [3D-Druck](#3d-druck)
- [Anfertigen der BambiKam Pro](#anfertigen-der-bambikam-pro)
    - [Lasern von Aviatik-Sperrholz 2mm](#lasern-von-aviatik-sperrholz-2mm)
    - [Lüfterzähne drucken](#l%C3%BCfterz%C3%A4hne-drucken)
    - [Kleben der einzelnen Elemente](#kleben-der-einzelnen-elemente)
        - [Abstandhalter auf der langen Grundplatte](#abstandhalter-auf-der-langen-grundplatte)
    - [Lackieren der BambiKam Pro](#lackieren-der-bambikam-pro)
        - [Lüfterzähne an die lange Grundplatte](#l%C3%BCfterz%C3%A4hne-an-die-lange-grundplatte)
- [Montage](#montage)
    - [Anbringen der unteren Platte](#anbringen-der-unteren-platte)
    - [Verlegen der Kabel](#verlegen-der-kabel)
    - [Sender und Antenne montieren](#sender-und-antenne-montieren)
    - [Montage der Kamera](#montage-der-kamera)
- [Konfiguration](#konfiguration)
    - [Programmieren des Gimbals](#programmieren-des-gimbals)
- [Anbringen der Grundplatte an den Kopter](#anbringen-der-grundplatte-an-den-kopter)
- [Fliegen](#fliegen)
- [Wichtige/wissenswerte Punkte](#wichtigewissenswerte-punkte)
- [Testflug](#testflug)

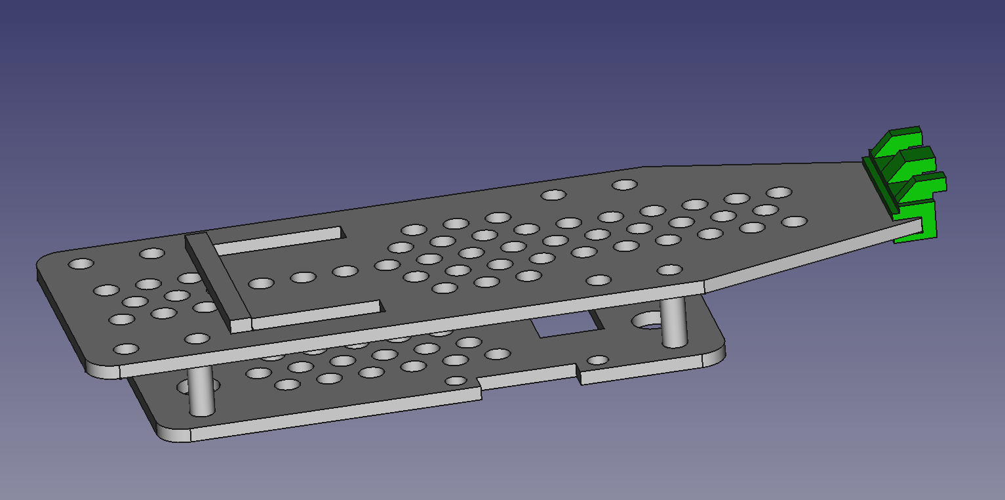
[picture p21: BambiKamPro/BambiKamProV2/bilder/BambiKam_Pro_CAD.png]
Bild der BambiKam Pro


## Was ist BambiKam?

BambiKam ist eine Plattform, welche es erlaubt eine [FLIR BOSON](http://www.flir.de/cores/boson/) Wärmebildkamera zusammen mit einem [Eachine TX801-Sender](https://www.google.com/search?q=eachine%20tx801) und einer [Cloverleaf](https://www.google.com/search?q=align+cloverleaf+5.8+ghz)-Antenne an eine [DJI Mavic Pro/Platinum](https://www.google.com/search?q=dji+mavic+pro+platinum) zu befestigen.

## Zeig her die Bilder! Ich will sehen wie's aussieht!

Links
Rechts
Vorne
Hinten
Oben
Unten

## Was zeichnet BambiKam Pro aus?

- Inklusive Kamera, Sender und Antenne beträgt das Gewicht ca. 120 Gramm. Gewicht
- Jederzeit perfekt ausbalancierte, senkrecht ausgerichtete Kameraeinstellung
- ...

## Müssen an der Drohne Modifikationen vorgenommen werden?

Durch die Tatsache, dass eine eigene Stromversorgung wiederum Gewicht bedeutet und schon eine Stromversorgung der Drohne vorhanden ist, welche verwendet werden kann, um den Sender und die Kamera mit Strom zu versorgen, ist es eine Überlegung wert, die Stromversorgung des Quadcopters anzuzapfen. Selbstverständlich muss man sich der Tatsache bewusst sein, dass dies Auswirkung auf die Herstellergarantie haben kann.

Der Stromverbrauch des Senders und der Kamera ist sehr klein und beeinflusst die Flugzeit minimal.

Die BambiKam Pro könnte einen kleinen Akku aufnehmen, wenn der Sender woanders platziert wird.

## Lizenz

BambiKam Pro steht unter der Lizenz [CC BY SA](https://creativecommons.org/licenses/by-sa/3.0/ch/) und darf somit beliebig kopiert, verändert und geteilt werden unter der Bedingung, dass diese Änderungen wiederum geteilt werden und ein Hinweis auf das Ursprungsprojekt gegeben wird.

Es wird keine Verantwortung übernommen.

## Materialien

### Aviatik-Sperrholz 2mm

Der Hauptteil besteht aus Aviatik Sperrholz, 2mm. Dieses erhält man bei Coop Bau&Hobby.
Das Aviatik Sperrholz hat den Vorteil, dass es dünn, sehr stabil und vielschichtig verleimt ist.

### 3D-Druck

Die Lüfterzähne für die Stabilitätserhöhung werden im 3D-Druckverfahren hergestellt.

## Anfertigen der BambiKam Pro

Ist das Holz beschafft, so lässt sich die Form sehr einfach mit einem LaserCutter schneiden.
Beispielsweise verfügen diverse Fablabs in der Schweiz über einen Lasercutter [Fablabs der Schweiz](https://fablab.ch/#/machine).
So auch das [FablabWinti](https://www.fablabwinti.ch/das-lab/ausstattung/lasercutter/). (Neue Mitglieder sind immer herzlich willkommen!)

### Lasern von Aviatik-Sperrholz 2mm



Das SVG [BambiKam_Pro_Aviatik_Sperrholz_2mm.svg](plan/BambiKam_Pro_Aviatik_Sperrholz_2mm.svg) soll folgendermassen gelasert werden:

| Reihenfolge | Farbe | Geschwindigkeit | Intensität |
| --- | --- | --- | --- |
| 1 | Gelb | 1000 | 3% |
| 2 | Pink | 1000 | 70% |
| 3 | Schwarz | 1000 | 70% |
| 4 | Rot | ignorieren | ignorieren |

> Bitte beachten, dass die Holzmaserung gemäss dem roten Pfeil ausgerichtet wird.

### Lüfterzähne drucken

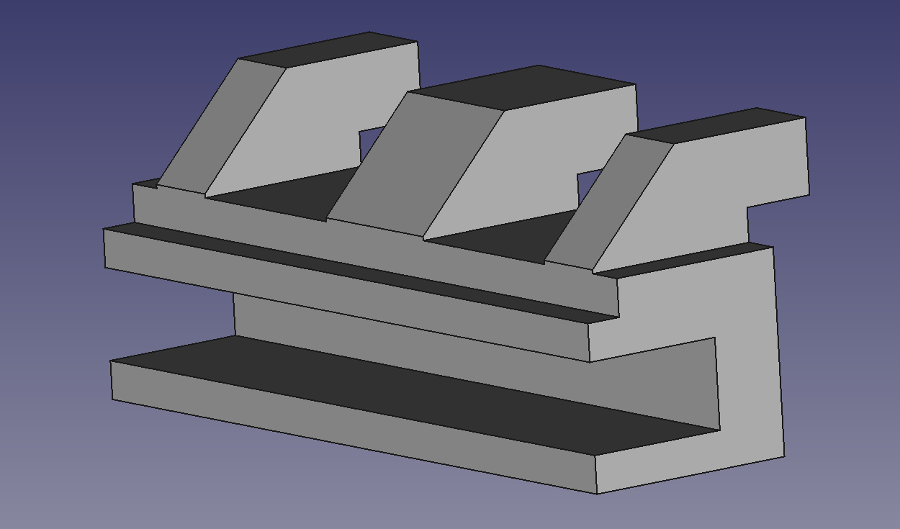
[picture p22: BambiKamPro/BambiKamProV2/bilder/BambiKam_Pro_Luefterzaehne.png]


Das STL [BambiKam_Pro_Luefterzaehne_3D-Druck.stl](plan/BambiKam_Pro_Luefterzaehne_3D-Druck.stl) kann mit dem 3D-Drucker ausgedruckt werden.

TODO: Braucht es da spezielle Einstellungen?

### Kleben der einzelnen Elemente

Um die einzelnen Elemente zu kleben, wird ein Sekundenleim empfohlen.

Beispielsweise UHU blitzschnell Supergel oder Pattex Ultra Gel. Beide zeichnen sich dadurch aus, dass sie auch outdoortauglich sind und sehr gut halten.

Wichtig ist anschliessend, das verleimte Produkt an der Luft zu trocknen: So verbleiben keine weissen Absonderungen des Sekundenleimes am Holz.

#### Abstandhalter auf der langen Grundplatte

Der Abstandhalter stellt einen Abstand zur Drohne her, damit unter dieser die Luft etwas besser zirkulieren kann.

Der Abstandhalter sollte gleich hinter den vertikalen Landekufen-Aussparungen angebracht werden. Die exakte Position ist im Bild ganz oben ersichtlich.

### Lackieren der BambiKam Pro

Um das Holz vor Feuchtigkeit zu schützen, kann die BambiKam Pro noch mit einem schützenden Klarlack lackiert werden. Die allenfalls zuvor schon angebrachten Elemente sollten aber entfernt werden.

#### Lüfterzähne an die lange Grundplatte

Die Lüfterzähne müssen ebenfalls nach oben zeigen und ganz vorne mittig an der Grundplatte festgeklebt werden.

## Montage

### Anbringen der unteren Platte

...
- Gimbalsteuerung auf kleine Grundplatte schrauben.
- Mittels Abstandhalter verbinden mit Grundplatte verbinden.

### Verlegen der Kabel

...

### Sender und Antenne montieren

>Es ist wichtig, dass die Antenne während des Betriebes nicht abfallen kann. Wird der Sender ohne Antenne betrieben, kann dieser beschädigt werden.

...

### Montage der Kamera

...

## Konfiguration

### Programmieren des Gimbals

1. Aufrufen der Seite
   <a href="https://www.basecamelectronics.com/downloads/8bit/" target="_blank">https://www.basecamelectronics.com/downloads/8bit/</a>
2. Version 2.2b2 mit Hex File Downloaden
3. Aus der Sektion 2.2b2 die folgenden Dateien herunterladen:
   - Die Firmware-Datei SimpleBGC_2_2b2.enc.hex
   - Das GUI SimpleBGC_GUI_2_2b2.zip 
4. Das GUI installieren.
5. Den Gimbal-Controller über USB-Kabel mit dem Computer verbinden.
6. Starten des GUIs.
7. Die Einstellungen gemäss folgenden Screenshots vornehmen:
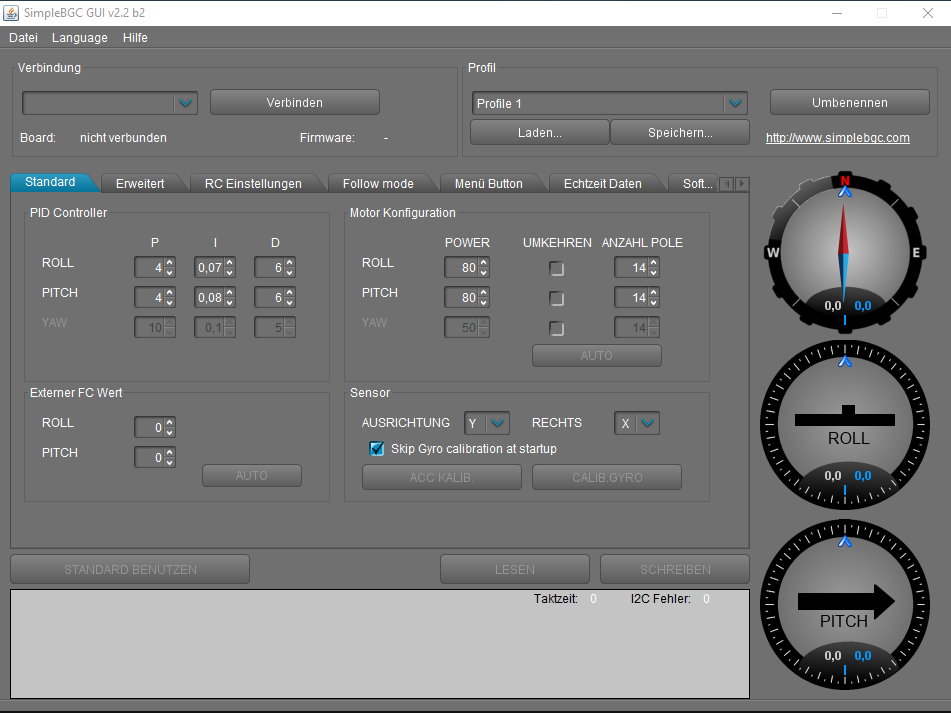
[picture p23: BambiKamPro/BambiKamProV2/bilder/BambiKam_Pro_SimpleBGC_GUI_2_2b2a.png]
Register Standard
   
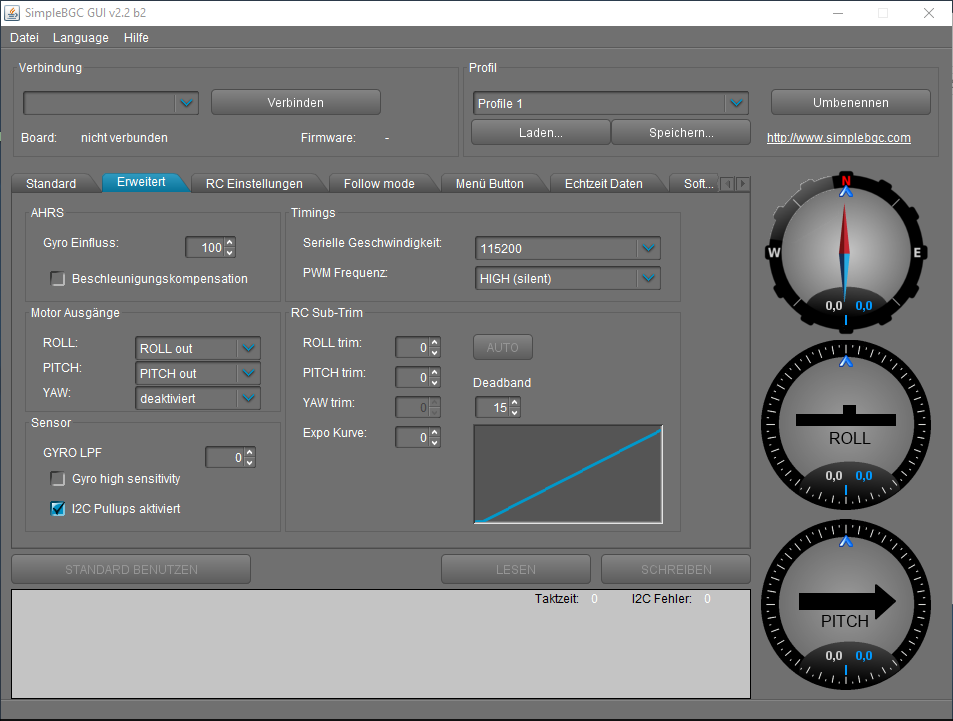
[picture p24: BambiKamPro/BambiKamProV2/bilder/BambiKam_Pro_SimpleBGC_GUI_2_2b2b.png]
Register Erweitert
   
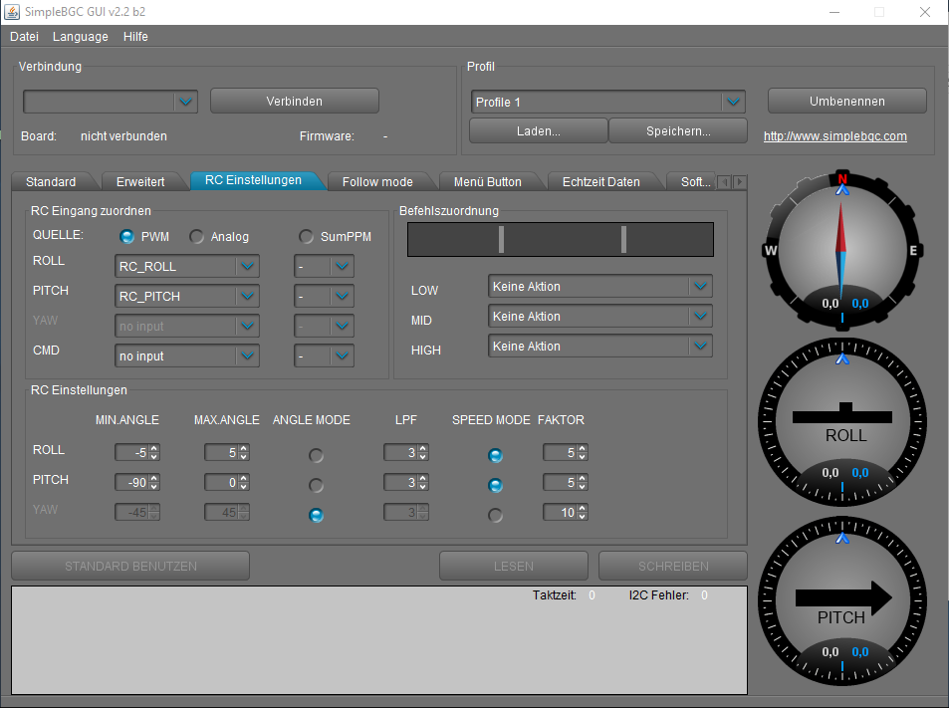
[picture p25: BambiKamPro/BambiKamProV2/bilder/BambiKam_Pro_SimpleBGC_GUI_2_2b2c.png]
Register RC Einstellungen
   
8. Kamera 90° manuell nach unten richten.
9. Anschliessend nacheinander "ACC KALIB“ "CALIB GYRO“ und „SCHREIBEN“ anwählen.

## Anbringen der Grundplatte an den Kopter

Am besten legt man die Mavic auf den Rücken und legt die Grundplatte so auf die Landekufen, dass sie durch die vertikalen Aussparungen zeigen. Die Befestigung der Grundplatte erfolgt durch das Einschieben des Splintens.

## Fliegen

Schalten Sie *vor* dem Abheben das "Vision Positioning System" aus. Sie finden dieses in den Einstellungen von Litchi unter dem Punkt "Vision Positioning System". Werden die Sensoren nicht deaktiviert, so wird die Mavic unsteuerbar steigen (ca. 10 Meter), bis das System eine Fehlfunktion der Sensoren erkennt und diese dann ignoriert.

Das Flugverhalten der Mavic wird durch das Mitführen der BambiKam Pro nicht gross verändert. Der Start verläuft balanciert, da sich die Komponenten im Schwerpunkt befinden.

## Wichtige/wissenswerte Punkte

- Der Sender darf *nie* ohne Antenne mit Strom versorgt werden, da sonst der Sender zerstört wird.
- Das an der Stromversorgung angehängte Kabel führt nur Strom, wenn die Drohne eingeschaltet ist. Ein Ein-/Aus-Schalter ist nicht nötig.
- Vor dem Start muss das "Vision Positioning System" deaktiviert werden.

## Testflug

| | |
| --- | --- |
| Datum: | 19.08.2018 10:35 |
| Wetter: | Wolkenloser Himmel, 22°C, Wind 5 km/h |
| Testszenario: | Wiederholter Wegpunktflug des folgenden Tracks: https://flylitchi.com/hub?m=hBNMMruee6# |
| Zeitmessung: | Ab Start des 1. Missionsdurchganges (ein Meter ab Boden) bis zum Ertönen des Akku-Alarms (30%) |
| __Erreichte Zeiten:__ | __14 Minuten 20 Sekunden__ (Ausrichtung des Kopters immer gleich) |
| __Erreichte Zeiten:__ | __14 Minuten 57 Sekunden__ (Vorwärtsflug) |

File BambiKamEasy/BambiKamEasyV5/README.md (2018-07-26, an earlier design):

# BambiKam V5 06.07.2018

- [Was ist BambiKam?](#was-ist-bambikam)
- [Warum wurde BambiKam entworfen?](#warum-wurde-bambikam-entworfen)
- [Zeig her die Bilder! Ich will sehen wie's aussieht!](#zeig-her-die-bilder-ich-will-sehen-wies-aussieht)
- [Was zeichnet BambiKam aus?](#was-zeichnet-bambikam-aus)
- [Müssen an der Drohne Modifikationen vorgenommen werden?](#m%C3%BCssen-an-der-drohne-modifikationen-vorgenommen-werden)
- [Lizenz](#lizenz)
- [Beschaffung der Materialien](#beschaffung-der-materialien)
    - [Aviatik-Sperrholz 2mm](#aviatik-sperrholz-2mm)
    - [Sperrholz 4mm](#sperrholz-4mm)
    - [Acrylglas/PMMA 2mm](#acrylglaspmma-2mm)
- [Anfertigen der BambiKam](#anfertigen-der-bambikam)
    - [Lasern der einzelnen Materialien](#lasern-der-einzelnen-materialien)
        - [Lasern von Aviatik-Sperrholz 2mm](#lasern-von-aviatik-sperrholz-2mm)
        - [Lasern von Sperrholz 4mm](#lasern-von-sperrholz-4mm)
        - [Lasern von Acrylglas/PMMA 2mm](#lasern-von-acrylglaspmma-2mm)
    - [Nachbearbeitung](#nachbearbeitung)
        - [Kamerahalter aus Acrylglas](#kamerahalter-aus-acrylglas)
        - [Elemente aus Aviatik-Sperrholz 2mm](#elemente-aus-aviatik-sperrholz-2mm)
    - [Kleben der einzelnen Elemente](#kleben-der-einzelnen-elemente)
        - [Abstandhalter auf Grundplatte (Mitte)](#abstandhalter-auf-grundplatte-mitte)
        - [Rohr auf Grundplatte (Rechts)](#rohr-auf-grundplatte-rechts)
        - [Mast auf Grundplatte (Links)](#mast-auf-grundplatte-links)
- [Montage der Elemente auf der Grundplatte](#montage-der-elemente-auf-der-grundplatte)
    - [Kamera montieren](#kamera-montieren)
    - [Sender und Antenne montieren](#sender-und-antenne-montieren)
    - [Verlegen der Kabel](#verlegen-der-kabel)
- [Anbringen der Grundplatte an den Kopter](#anbringen-der-grundplatte-an-den-kopter)
- [Fliegen](#fliegen)
- [Wichtige/wissenswerte Punkte](#wichtigewissenswerte-punkte)

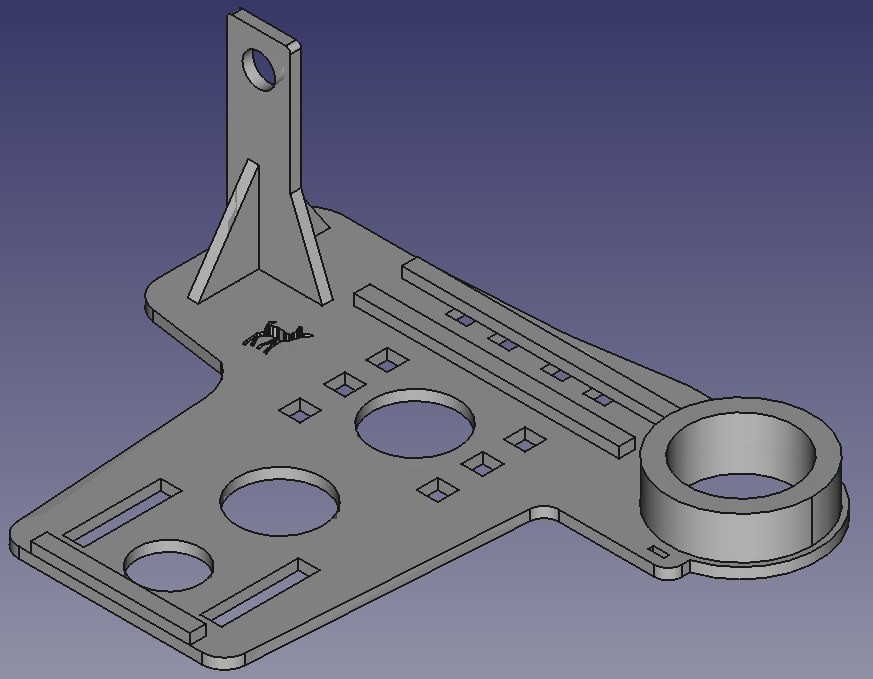
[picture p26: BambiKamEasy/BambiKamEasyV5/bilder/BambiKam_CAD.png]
Bild der BambiKam


## Was ist BambiKam?

BambiKam ist eine Plattform, welche es erlaubt eine [FLIR BOSON](http://www.flir.de/cores/boson/) Wärmebildkamera zusammen mit einem [Eachine TX801-Sender](https://www.google.com/search?q=eachine%20tx801) und einer [Cloverleaf](https://www.google.com/search?q=align+cloverleaf+5.8+ghz)-Antenne an eine [DJI Mavic Pro/Platinum](https://www.google.com/search?q=dji+mavic+pro+platinum) zu befestigen.

## Warum wurde BambiKam entworfen?

BambiKam wurde für die Rehkitzsuche entworfen. Damit die Mavic mit dem Velo transportiert werden könnte, ist es wichtig, dass sie nicht mehr Platz braucht als wirklich nötig. Die Mavic kann so im nicht gefalteten Zustand in einen Koffer verstaut werden.

## Zeig her die Bilder! Ich will sehen wie's aussieht!

Links
Rechts
Vorne
Hinten
Oben
Unten

## Was zeichnet BambiKam aus?

- Inklusive Kamera, Sender und Antenne beträgt das Gewicht weniger als 60 Gramm. Gewicht
- Durch das Anbringen der Kamera, Sender und Antenne auf der Seite kann auf Fussverlängerungen verzichtet werden. Dies spart ebenfalls Gewicht und macht die Drohne nicht höher.
- Durch die einfache Befestigung der Grundplatte an den hinteren Landekufen der Mavic ist es ganz einfach, die BambiKam zu entfernen und die Drohne als ganz normale Drohne zu verwenden.
- Die Grundplatte hat Löcher, welche die Sensoren der Mavic nicht beeinträchtigen. So ist es möglich, auch nach dem Anbringen der BambiKam, die Mavic mit Hilfe der Sensoren zu landen.

## Müssen an der Drohne Modifikationen vorgenommen werden?

Durch die Tatsache, dass eine eigene Stromversorgung wiederum Gewicht bedeutet und schon eine Stromversorgung der Drohne vorhanden ist, welche verwendet werden kann, um den Sender und die Kamera mit Strom zu versorgen, ist es eine Überlegung wert, die Stromversorgung des Quadcopters anzuzapfen. Selbstverständlich muss man sich der Tatsache bewusst sein, dass dies Auswirkung auf die Herstellergarantie hat.

Der Stromverbrauch des Senders und der Kamera ist sehr klein und beeinflusst die Flugzeit minimal.

## Lizenz

BambiKam steht unter der Lizenz [CC BY SA](https://creativecommons.org/licenses/by-sa/3.0/ch/) und darf somit beliebig kopiert, verändert und geteilt werden unter der Bedingung, dass diese Änderungen wiederum geteilt werden und ein Hinweis auf das Ursprungsprojekt gegeben wird.

Es wird keine Verantwortung übernommen.

## Beschaffung der Materialien

### Aviatik-Sperrholz 2mm

Der Hauptteil besteht aus Aviatik Sperrholz, 2mm. Dieses erhält man bei Coop Bau&Hobby.
Das Aviatik Sperrholz hat den Vorteil, dass es dünn, sehr stabil und vielschichtig verleimt ist.

### Sperrholz 4mm

Die runden Elemente für die Kamerahalterung sind aus normalem 4mm Sperrholz, was nicht so dicht ist wie das Aviatik-Sperrholz.

### Acrylglas/PMMA 2mm

Die Kamerahalterung ist aus 2mm Acrylglas gefertigt und passt für das [Low Profile Boson VPC von OEMCAMERAS](https://www.oemcameras.com/rhp-bos-vpc-if.htm). Der Lochabstand beträgt 18mm.

## Anfertigen der BambiKam

Sind die Materialien beschafft, so lässt sich die Form sehr einfach mit einem LaserCutter schneiden.
Beispielsweise verfügt das [FablabWinti](https://www.fablabwinti.ch/das-lab/ausstattung/lasercutter/) über einen LaserCutter. (Neue Mitglieder sind immer herzlich willkommen!)

### Lasern der einzelnen Materialien

#### Lasern von Aviatik-Sperrholz 2mm



Das SVG [BambiKam_V5_Aviatik_Sperrholz_2mm.svg](plan/BambiKam_V5_Aviatik_Sperrholz_2mm.svg) soll folgendermassen gelasert werden:

| Reihenfolge | Farbe | Geschwindigkeit | Intensität |
| --- | --- | --- | --- |
| 1 | Gelb | 1000 | 3% |
| 2 | Türkis | 1000 | 75% |
| 3 | Hellgrün | 1000 | 75% |
| 4 | Pink | 1000 | 75% |
| 5 | Schwarz  | 1000 | 75% |

#### Lasern von Sperrholz 4mm



Das SVG [BambiKam_V5_Sperrholz_4mm.svg](./plan/BambiKam_V5_Sperrholz_4mm.svg) soll folgendermassen gelasert werden:

| Reihenfolge | Farbe | Geschwindigkeit | Intensität |
| --- | --- | --- | --- |
| 1 | Pink | 1000 | 60% |
| 2 | Schwarz | 1000 | 60% |

#### Lasern von Acrylglas/PMMA 2mm



Das SVG [BambiKam_V5_Kamerahalter_Acrylglas_2mm.svg](plan/BambiKam_V5_Kamerahalter_Acrylglas_2mm.svg) soll folgendermassen gelasert werden:

Für den einfachen Halter:

| Reihenfolge | Farbe | Geschwindigkeit | Intensität |
| --- | --- | --- | --- |
| 1 | Pink | 1000 | 50% |
| 2 | Schwarz | 1000 | 50% |

Für den Halter, der die Kamera ganz umfasst:

| Reihenfolge | Farbe | Geschwindigkeit | Intensität |
| --- | ----- | --- | --- |
| 1 | Blau  | 1000 | 50% |
| 2 | Rot | 1000 | 50% |

### Nachbearbeitung

Die einzelnen Elemente müssen nach dem Lasern nachbearbeitet werden, damit diese passen:

#### Kamerahalter aus Acrylglas

Die Löcher müssen mit einem 1.5er Bohrer nachgebohrt werden, bis die Schrauben der FLIR Boson gut reinpassen.

#### Elemente aus Aviatik-Sperrholz 2mm

##### Kleine Scheibe mit Loch mit Durchmesser 7 mm

Die kleine Scheibe mit Loch (Durchmesser von 7 mm) muss mit einem Schleifpapier soweit flach geschliffen werden, dass diese auf den Mast aufgelegt dem Sender und der Antenne guten Halt bietet. Erfahrungsgemäss sollte die Dicke knapp 1 mm betragen.

### Kleben der einzelnen Elemente

#### Abstandhalter auf Grundplatte (Mitte)

Die Abstandhalter stellen einen Abstand zur Drohne her, damit unter dieser die Luft etwas besser zirkulieren kann und zusätzlich die Kabel zwischen der Grundplatte und der Drohne durchgeführt werden können.

Die Orte, wo die Abstandhalter angebracht werden könnten, sind oben in den Bildern ersichtlich.

#### Rohr auf Grundplatte (Rechts)

Auf die Grundplatte werden zwei Sperrholzringe (Dicke 4mm, Durchmesser 2cm) auf das Loch geklebt. Es ist wichtig darauf zu achten, dass die Übergänge möglichst nicht spürbar sind und ein durchgängiges Loch mit dem Durchmesser von 2cm entsteht.

Es kann hierzu ein herkömlicher Holzleim verwendet werden.

Sollte sich die Kamera nicht leicht einschieben lassen, so kann mit einem ganz feinen Schleifpapier die vielleicht noch vorhanden Unebenheiten weggeschliffen werden.

#### Mast auf Grundplatte (Links)

Die Stützelemente und der eigentliche Mast, worauf noch die kleine Scheibe mit Durchmesser 6mm angebracht wird, bilden die Halterung für den Sender und die Antenne.

Da die Elemente voneinander abhängen und relativ rasch halten müssen, empfiehlt es sich hier einen holztauglichen Sekundenleim zu verweden.
Wichtig ist, an der Luft trocknen: So verbleiben keine weissen Absonderungen des Sekundenleimes am Holz.

## Montage der Elemente auf der Grundplatte

### Kamera montieren

Der Kamerahalter wird auf der Seite montiert, wo die Buchse angebracht ist, welche mit der Öffnung nach oben zeigt.

Der Kamerahalter wird mit den mitgelieferten Schrauben befestigt und mit Kabelbindern an der Grundplatte befestigt.

Es werden dabei zwei Kabelbinder benötigt:

- Einem Kabelbinder wird der Binderkopf so zerschnitten, dass noch ein wenig davon übersteht und als Begrenzung dient.
- Einem weiteren Kabelbinder wird der Binderkopf komplett abgeschnitten.

Die Kamera wird anschliessend mit der Linse nach unten und der Kamerahalterung Richtung Heck in das Loch eingelegt. (Falls es nicht passt, wie oben beschrieben, mit einem Streifen feinem Schleifpapier etwas nachschleifen.)

Der Kabelbinder mit dem teilweise abgeschnittenen Binderkopf von oben durch das Loch schieben und unterhalb der Grundplatte mit dem Binderkopf fixieren.

### Sender und Antenne montieren

Die holzige Unterlagscheibe, welche schon flachgeschliffen wurde, am Mast anbringen und gut anziehen. Die Antenne soll dabei nach vorne zeigen.

*Es ist wichtig, dass die Antenne während des Betriebes nicht abfallen kann. Wird der Sender ohne Antenne betrieben, kann dieser beschädigt werden.*

### Verlegen der Kabel

Die Kabel können durch den doppelt vorhandenen Abstandhalter gelegt werden und der Einfachheit halber einfach mit einem Streifen Klebeband befestigt werden.

## Anbringen der Grundplatte an den Kopter

Am besten legt man die Mavic auf den Rücken und legt die Grundplatte mit der Kamera nach unten zeigend so auf die Landekufen, dass sie durch die vertikalen Aussparungen zeigen. Die Befestigung der Grundplatte erfolgt durch das Einschieben des Splintens mit der Aussparung. Wichtig ist, dass der Splinten von links eingeschoben wird, da so die Kamera nicht verdeckt wird.

## Fliegen

Das Flugverhalten der Mavic wird durch das Mitführen der BambiKam nicht merklich verändert. Der Start verläuft balanciert, da sich die Komponenten im Schwerpunkt befinden.

Durch das geringe Gewicht der BambiKam wird auch die Flugzeit nicht allzu negativ beeinflusst.

## Wichtige/wissenswerte Punkte

- Der Sender darf *nie* ohne Antenne mit Strom versorgt werden, da sonst der Sender zerstört wird.
- Das an der Stromversorgung angehängte Kabel führt nur Strom, wenn die Drohne eingeschaltet ist. Ein Ein-/Aus-Schalter ist nicht nötig.

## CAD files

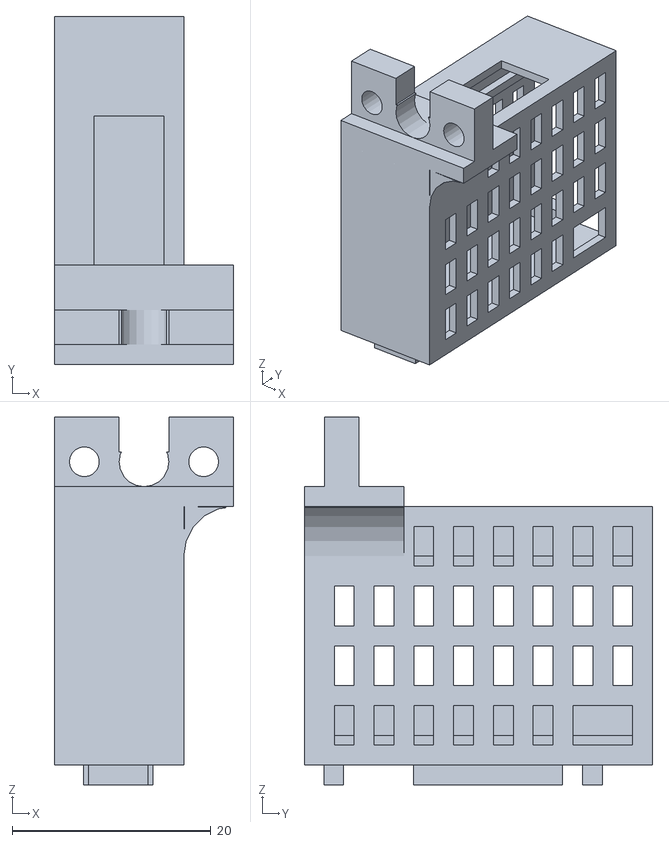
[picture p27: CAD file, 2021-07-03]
BambiKamEasy/BambiKamEasyV8.11/plan/BambiKam_Easy_Transmittergehaeuse_TBS_Unify_Pro_5G8_HV_3D-Druck.stl
18.0 x 35.0 x 37.0

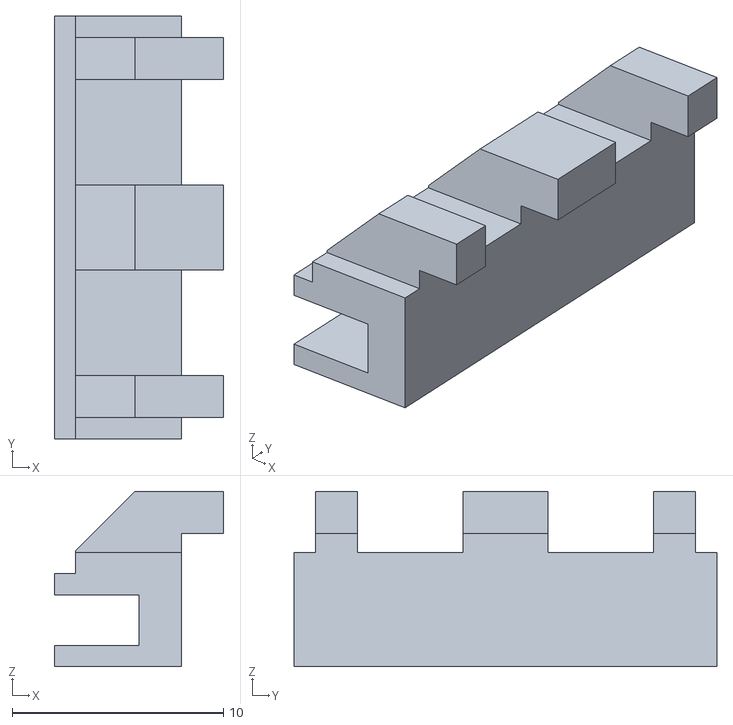
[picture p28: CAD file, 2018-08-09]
BambiKamPro/BambiKamProV2/plan/BambiKam_Pro_Luefterzaehne_3D-Druck.stl
8.00 x 20.0 x 8.30

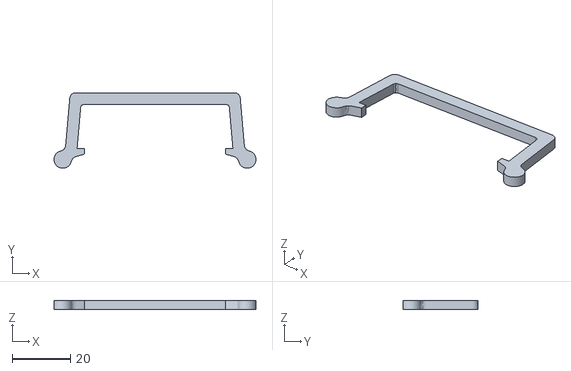
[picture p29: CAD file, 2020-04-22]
BambiKamEasy/BambiKamEasyV8.11/plan/BambiKam_Easy_Splinten_fuer_Mavic2.stl
69.1 x 25.8 x 3.00

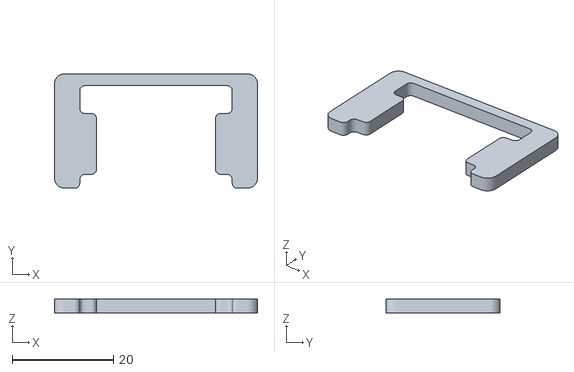
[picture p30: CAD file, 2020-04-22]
BambiKamEasy/BambiKamEasyV8.11/plan/BambiKam_Easy_Splinten_fuer_Mavic1.stl
40.1 x 22.6 x 2.80

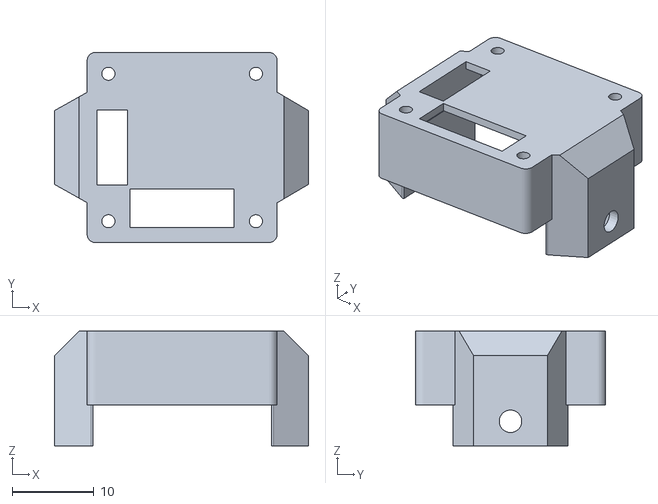
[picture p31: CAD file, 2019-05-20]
BambiKamEasy/BambiKamEasyV8.11/plan/BambiKam_Easy_Kameragehaeuse_3D-Druck_FLIR_BOSON_RCIF_320-640.stl
31.0 x 23.2 x 14.0

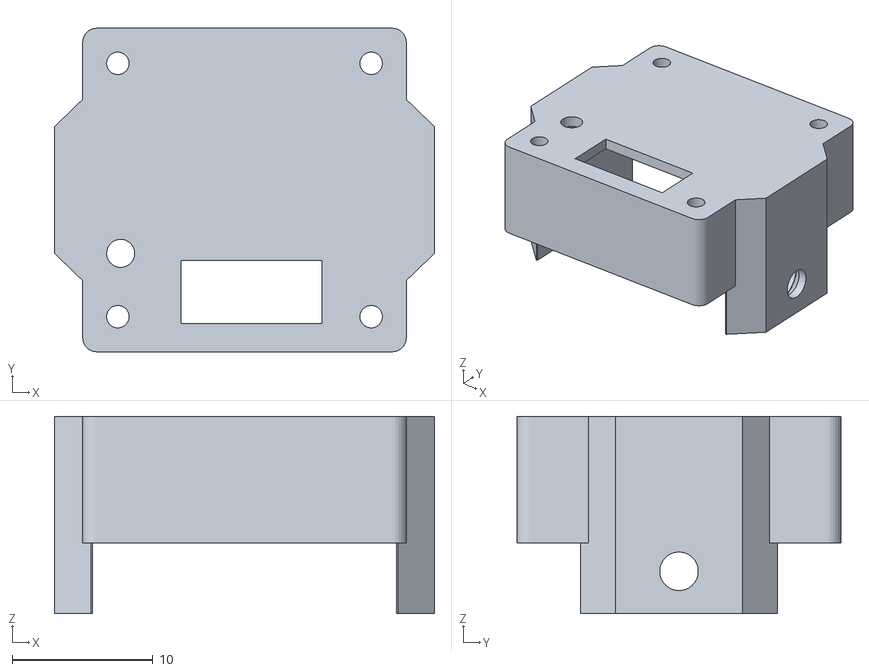
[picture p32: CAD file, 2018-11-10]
BambiKamEasy/BambiKamEasyV8.11/plan/BambiKam_Easy_Kameragehaeuse_3D-Druck_FLIR_BOSON_LowIF_320.stl
27.0 x 23.0 x 14.0

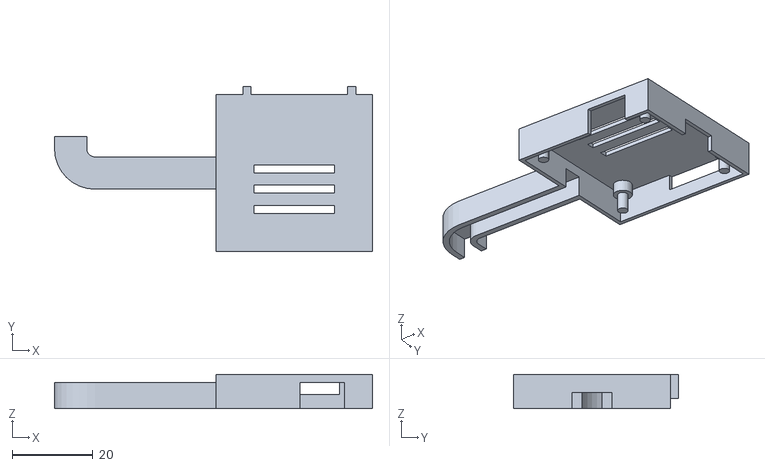
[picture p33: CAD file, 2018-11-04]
BambiKamEasy/BambiKamEasyV8.11/plan/BambiKam_Easy_Transmittergehaeuse_SpeedyBee_VTX-DVR-Boden-3D-Druck.stl
78.8 x 40.8 x 8.50

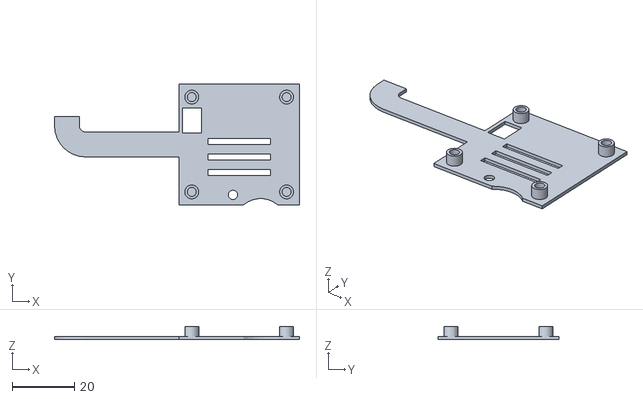
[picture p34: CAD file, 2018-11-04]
BambiKamEasy/BambiKamEasyV8.11/plan/BambiKam_Easy_Transmittergehaeuse_SpeedyBee_VTX-DVR-Deckel-3D-Druck.stl
78.8 x 38.8 x 4.25

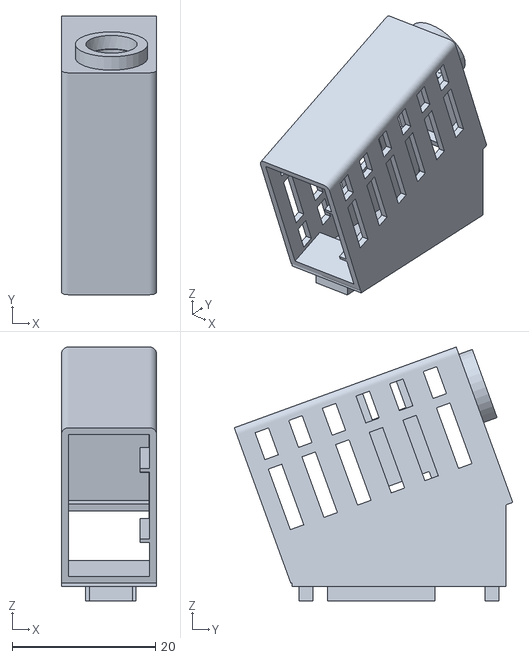
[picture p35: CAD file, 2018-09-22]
BambiKamEasy/BambiKamEasyV8.11/plan/BambiKam_Easy_Transmittergehaeuse_Eachine_TX801_3D-Druck.stl
13.3 x 38.9 x 35.5

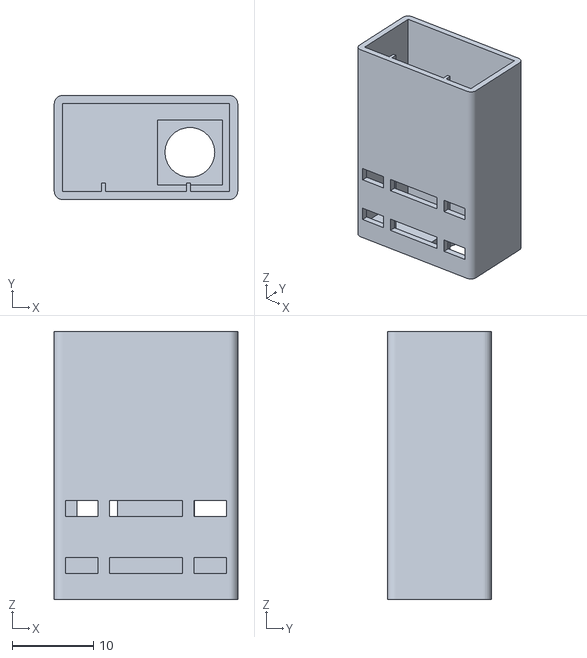
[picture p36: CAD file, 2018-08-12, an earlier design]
BambiKamEasy/BambiKamEasyV6/plan/BambiKam_Easy_Transmittergehaeuse_3D-Druck.stl
22.6 x 12.8 x 33.0

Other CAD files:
BambiKamEasy/BambiKamEasyV8.11/plan/BambiKam_Easy_Kameragehaeuse_3D-Druck_FLIR_BOSON_LowIF_640.stl
